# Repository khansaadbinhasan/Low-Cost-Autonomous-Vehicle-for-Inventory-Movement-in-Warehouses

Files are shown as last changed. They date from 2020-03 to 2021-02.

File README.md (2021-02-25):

# Low-Cost Autonomous Vehicle for Inventory Movement in Warehouses

* [__Project Objectives__](#project-objectives)
* [__Our Model__](#our-model)
* [__Evaluation Parameters__](#evaluation-parameters)
* [__Evaluating Model__](#evaluating-model)
* [__About this repository__](#about-this-repository)
* [__Conclusion and Further work__](#conclusion-and-further-work)
* [__More Information__](#more-information)

## Project Objectives

Automation can help Warehouses become more efficient, productive, robust, and cost-effective. A variety of Autonomous Robots are used in large warehouses which can be expensive. We intend to build cost-effective Autonomous Robots for small and medium scale Warehouses with reasonable accuracy.

## Our Model

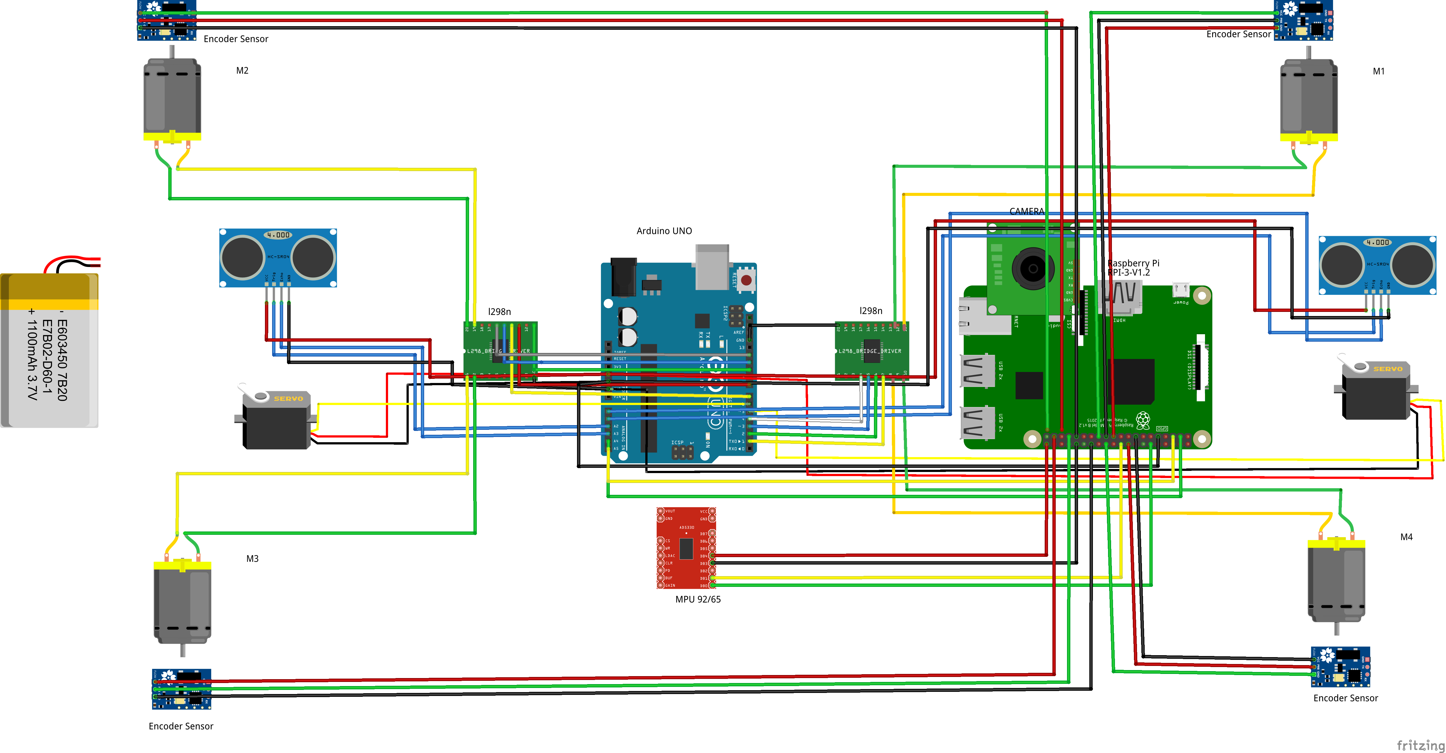
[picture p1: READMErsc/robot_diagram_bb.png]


The robot is monitored by the camera, which sends the stream to the workstation. Using the procedure described below, the workstation sends a command(UP, DOWN, LEFT, RIGHT) to the rpi via a TCP connection. The rpi then sends this command to the Arduino. The Arduino then sends a message to motor drivers accordingly. IMUs and Wheel Encoders are attached to the robot, which sends data to the rpi via an I2C connection. The Arduino is also connected to two servo motors mounted at the front and back. Two ultrasonic sensors are also connected to the servos. This arrangement can be used for backup and collision avoidance.

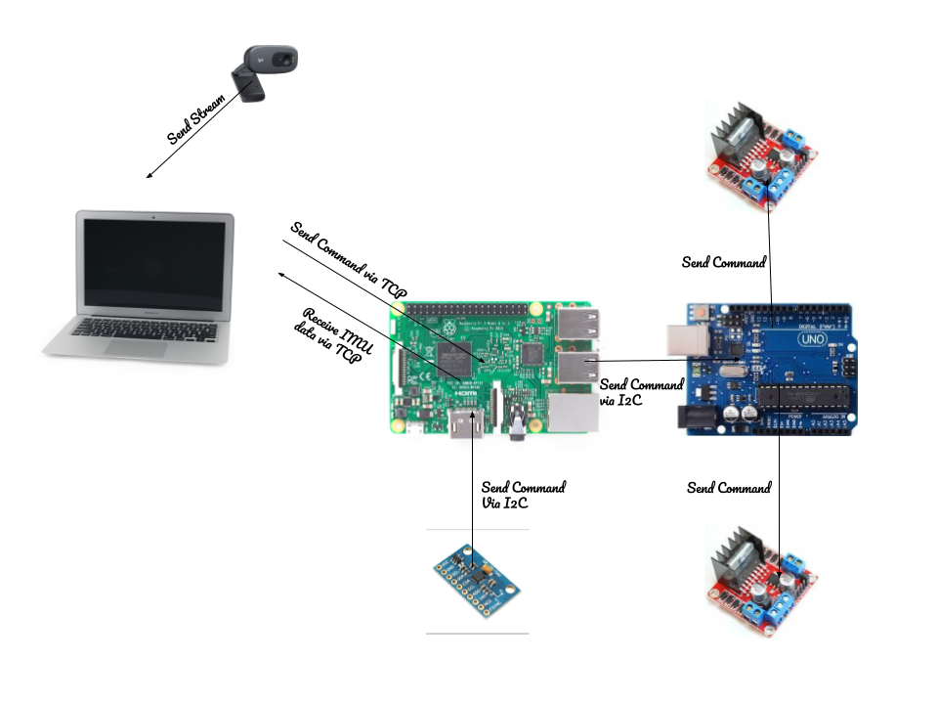
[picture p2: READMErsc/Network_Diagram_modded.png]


The Source and Destination are provided by the user in the environment visible to the camera. A path is made from source to destination using the A-star Algorithm.
A colored marker is placed on the robot which is used to estimate the robot’s location and the heading. A line is drawn from the yellow to the purple marker which gives the Heading. The decision to move the next step is taken using the heading of the robot, the robot’s current location, and the next coordinate in the path to follow. 

<p align="center">
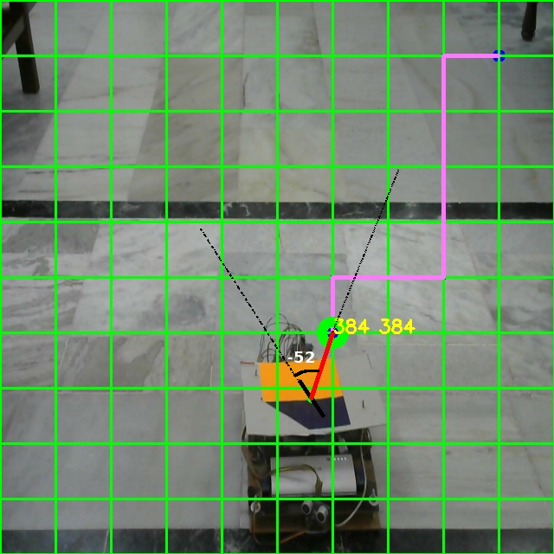
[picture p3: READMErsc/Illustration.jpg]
  
</p>

## Evaluation Parameters

* **Cost and Accuracy:** There is a trade-off between the accuracy of the robot and the cost required to build it. 
* **Scalability:** Using an overhead camera for tracking, robots can easily be scaled up, to track and guide multiple robots.
* **Backup system:** Redundancy should be available that could be used in case of any failure with the primary system. 
* **Path Following and Reaching Destination:** To track the deviation while the robot is traversing the estimated path and check whether the robot can reach the destination or not. 

## Evaluating Model 

We Evaluate the results on the success rate of the robot in reaching the destination and the deviation in the path to reach the destination. We have considered that if the distance between the robot and destination is less than 20cm or 100px, then the robot is on the destination point. We draw the path that the robot should move on and the path that the robot moved on. We compare these paths to measure how close the robot was to the destination.
The computed path is shown in orange color and the actual path traversed by the robot is shown using the blue color. 

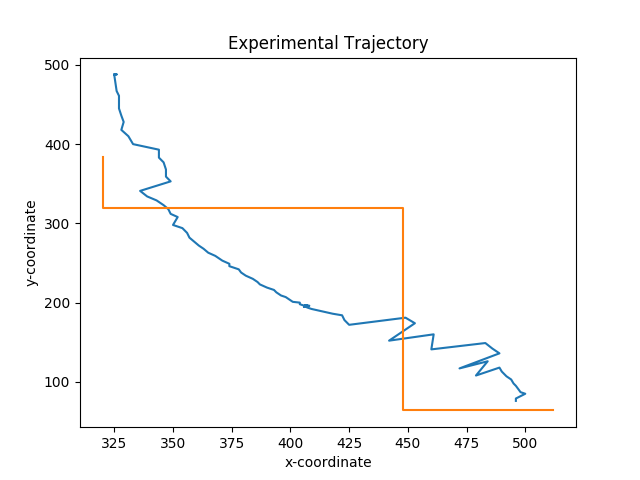
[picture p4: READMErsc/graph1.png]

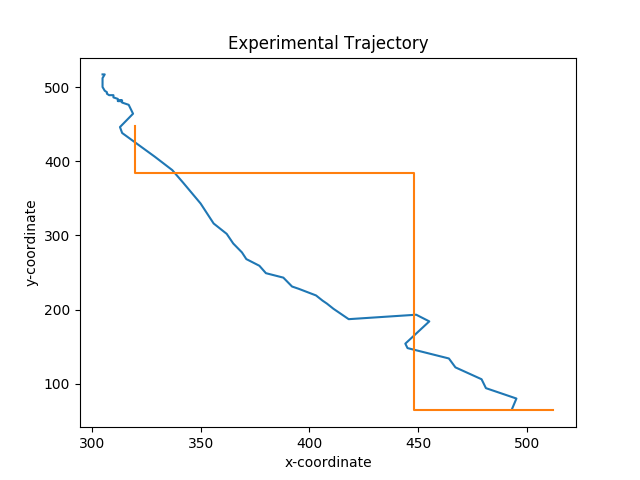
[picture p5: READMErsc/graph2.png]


Out of 10 times, The robot was able to reach the destination 6 times. Hence, the accuracy of our model should be close to 60%. The robot is built with cheap hardware which is easily available making our robot very affordable. The robot also uses an overhead camera which facilitates greater scalability

## About this repository

* **rsc** contains images and other files used for aid in building the model and documenting the work.
* **src** contains the source code of the project consisting of three folders:
	* **Arduino** contains the code to be uploaded to Arduino. Arduino further contains three folders:
		* **Misc Codes** contains code that was used to learn about libraries. Most of these are taken from tutorials easily found online. It also contains code that is no longer used in the robot but was used for testing at some point. It contains code to get data from ultrasonic sensors, move servos, move motors, etc.
		* **libs** contain the libraries that were used in the Arduino Project.
		* **Important** contains the code that was at some point used in the project and still holds importance. It can be used to test various parts of the robot. For example- to move the robot, rotate ultrasonic sensors, etc.

	* **Workstation** contains two folders:
		* **Important** contains the final code that was used in the workstation. 
		* **Misc Codes** contains code that was used to learn about modules and to test the robot. Some of the code was previously used.

	* **rpi** contains two folders:
		* **Important** contains the final code that was used in the raspberry pi.
		* **Misc Codes** contains code that was used to learn about modules and to test the robot. Some of the code was previously used.

* Upload `Major-Project/src/Arduino/important/MotionWithRotatingHCSR04/MotionWithRotatingHCSR04.ino` to Arduino UNO.
* Upload `src/rpi/Important/master.py` to raspberry pi and run it. This would wait for a connection to the address specified in the code. 
* Connect a camera to the workstation and place it so that the robot is clearly visible.
* Run `Major-Project/src/Workstation/Important/Obstacle Detection and Path Planning/main2.py`, you may want to configure the `IP address` and `port` in `parameters.py` as well. 
* A window will appear showing the stream from the camera. Double-click on the window at the starting point of the robot and the destination. Press `Esc`. Now a path appears and the robot starts moving toward the destination. The robot should move as shown in [this video](https://www.youtube.com/watch?v=GJ0nYhXhNK4&list=PLMkePoybCpm4CkMRtGrQV7CXr9gtPblFH&index=5)

## Conclusion and Further work

We have built a cheap and fairly accurate robot. It is versatile and can work in varied environments. Given the backup system and an overhead camera, the robot is fairly secure and scalable. The scope of the work can be enhanced in the future by employing novel ways of increasing accuracy with little changes in cost.

## More Information

* Please see my [Project Report](https://docs.google.com/document/d/1Ga6hZdya4-FO2D3pxWp_QicPi5e_mkiPZHorXCSN8MU/edit?usp=sharing) for more detailed information about this project. 
* A paper was also published in [PDGC 2020](https://www.juit.ac.in/pdgc-2020/index1.php) titled _**"Low-Cost Autonomous Vehicle for Inventory Movement in Warehouses"**_ You can Find it [here](https://ieeexplore.ieee.org/document/9315762). Please cite as `F. Alam, K. S. Bin Hasan and A. Varshney, "Low-Cost Autonomous Vehicle for Inventory Movement in Warehouses," 2020 Sixth International Conference on Parallel, Distributed and Grid Computing (PDGC), Waknaghat, India, 2020, pp. 400-405, doi: 10.1109/PDGC50313.2020.9315762.`
* Please refer to [this playlist](https://www.youtube.com/playlist?list=PLMkePoybCpm4CkMRtGrQV7CXr9gtPblFH) to learn more about the robot.
* You can also find the [presentation for the paper](https://www.slideshare.net/khansaadbinhasan/lowcost-autonomous-vehicle-for-inventory-movement-in-warehouses)

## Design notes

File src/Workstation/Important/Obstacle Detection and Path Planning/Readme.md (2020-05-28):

Dependencies to install <br/>
python3 -m pip install --user opencv-contrib-python</br>
<br/>
Steps <br/>
1. To run - python3 main2.py<br/>
2. It will ask the grid size, frame height, ,frame width, whether you want to detect obstacle in that frame or not.
3. Then select the two points one as source and other as destination<br/>
4. Black colour objects will be treated as obstacles.<br/>
5. Then the next window will be opened, with the help of the mouse pointer,  select the region of the frame that you want to track and then press enter<br/>

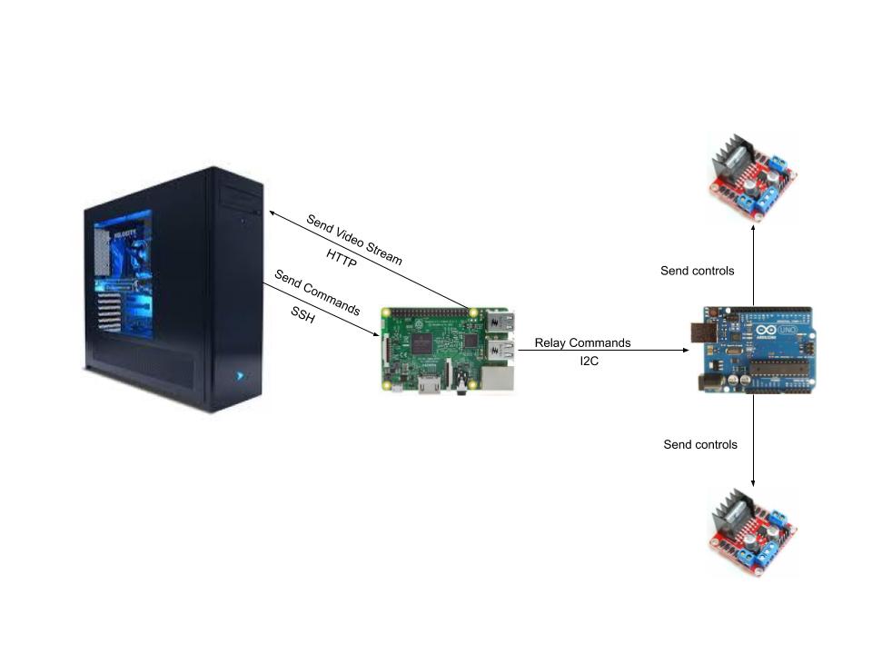
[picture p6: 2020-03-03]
rsc/System Overview.jpg

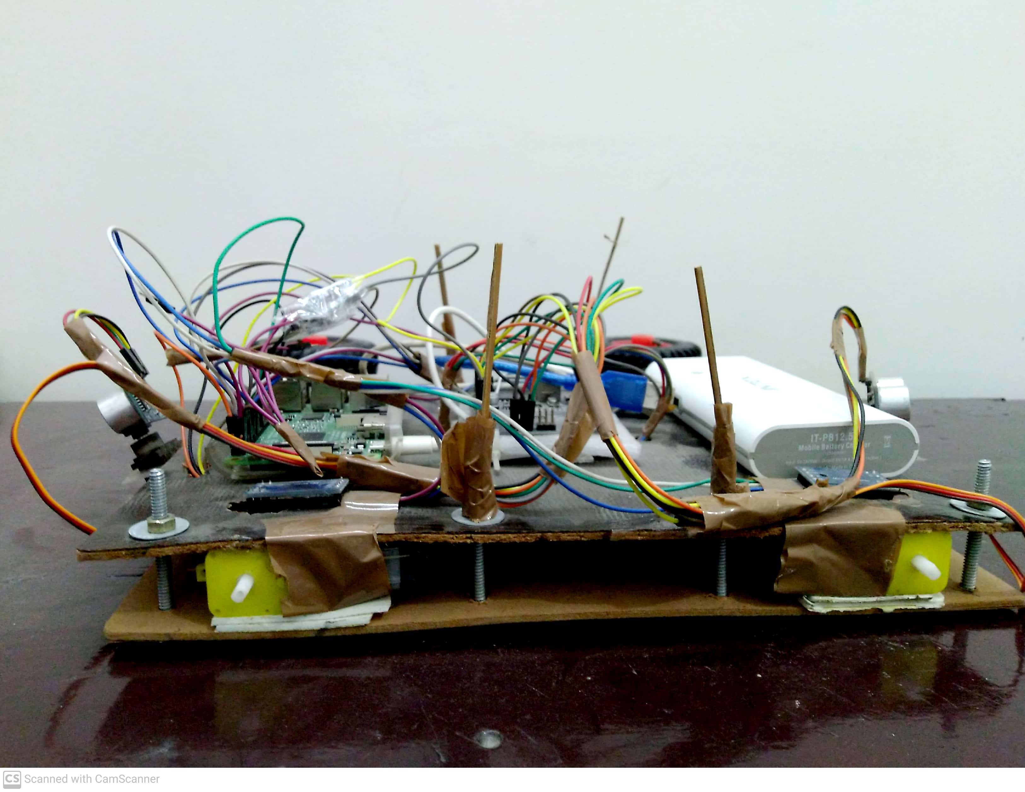
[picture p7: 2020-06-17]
rsc/Photos/project_2.jpg

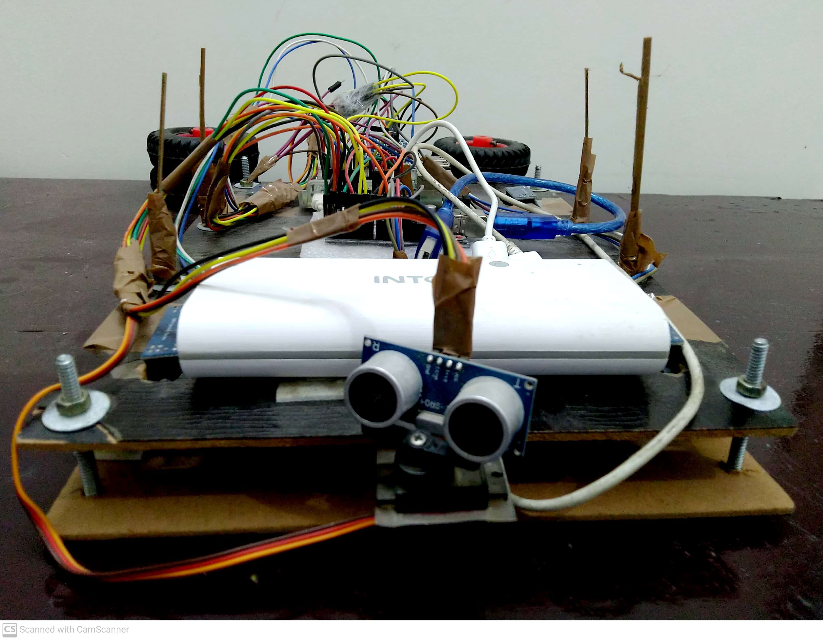
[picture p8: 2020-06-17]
rsc/Photos/project_3.jpg

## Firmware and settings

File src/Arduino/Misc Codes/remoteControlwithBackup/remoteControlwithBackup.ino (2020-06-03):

/*
  --> Uses A4 and A5 pins of arduino and connects according to /rsc/i2c.jpg
  --> This sketch helps in I2C communication with the raspberry pi, receives command from the pi and sends ACK to it
  --> This sketch runs motors in different directions according to commands received via I2C from rpi.
  --> After setting up the Robot, upload this sketch to arduino.
  --> This can be used to test if remote control is working or not
*/

/*  Temperature(*C) Table for ultrasonic sound

Temp, T(*C)     Speed, v(m/s)

T < 10        331 + 0.6*T
10 < T < 20     331 + 0.6*T
20 < T < 30     331 + 0.6*T
30 < T < 40     331 + 0.6*T
40 < T < 50     331 + 0.6*T
Over          336 + 0.1*T

*/


#include <Servo.h>
#include <Wire.h>

#define SLAVE_ADDRESS 0x04


Servo servo_forward;
Servo servo_backward;


// pin numbers for HC-SR04, 1 is front, 2 is back
#define trigPin_backward A0
#define echoPin_backward A1

#define trigPin_forward A2
#define echoPin_forward A3

#define powerPin 9


// pin numbers for Servos, 1 is front, 2 is back
#define servoPin_forward 5
#define servoPin_backward 6


// variables

// Defining different directions for the robot
const int forward = 1;
const int backward = 2;

// commands to move the robot in different directions
int STOP = 0;
int UP = 1;
int DOWN = 2;
int RIGHT = 3;
int LEFT = 4;

int cmd = STOP;


// motor driver front
// motor one
int input_front1 = 2;
int input_front2 = 4;


// motor two
int input_front3 = 7;
int input_front4 = 8;


// motor driver 2
// motor three
int input_back3 = 12;
int input_back4 = 13;


// motor four
int input_back1 = 10;
int input_back2 = 11;


// Variables for HC-SR04 sensor
long duration_backward;
int distance_backward;
long duration_forward;
int distance_forward;

int currentTemp = 25;
const int v = 331 + 0.6*currentTemp;
const int upper_HCSR04_limit = 400;
const int lower_HCSR04_limit = 2;


// Variables for Servo
// const int defaultAng = 90;
const int minAng = 0;
const int maxAng = 180;
const int midAng = ( maxAng - minAng ) / 2;

int servoang_front = midAng;
int servoang_back = midAng;

int i = 0;
int j = 0;


// For Backup
int safetyDist = 10;
int robotSafe = 1;
int letRun = 0;
int wireIn = -1;

void setup() 
{
  //Setting up the I2C connections
  Wire.begin(SLAVE_ADDRESS);
  Wire.onReceive(receiveData);
  Wire.onRequest(sendData);


  //motor drive 1
  // motor 1
  pinMode(input_front1, OUTPUT);
  pinMode(input_front2, OUTPUT);
  
  // motor 2
  pinMode(input_front3, OUTPUT);
  pinMode(input_front4, OUTPUT);


  //motor drive 2
  // motor 3
  pinMode(input_back3, OUTPUT);
  pinMode(input_back4, OUTPUT);
  
  // motor 4
  pinMode(input_back1, OUTPUT);
  pinMode(input_back2, OUTPUT);


  //HCSR04 pins, 1 is front 2 is back
  pinMode(trigPin_backward, OUTPUT); // Sets the trigPin as an Output
  pinMode(echoPin_backward, INPUT); // Sets the echoPin as an Input

  pinMode(trigPin_forward, OUTPUT); // Sets the trigPin as an Output
  pinMode(echoPin_forward, INPUT); // Sets the echoPin as an Input

  pinMode(powerPin, OUTPUT); // Sets the echoPin as an Input


  //Servo pins, 1 is front 2 is back
  servo_forward.attach(servoPin_forward, minAng, maxAng );
  servo_backward.attach(servoPin_backward, minAng, maxAng );

  Serial.begin(115200); // Starts the serial communication
}



void update_distances()
{
  // Clears the trigPin
  digitalWrite(trigPin_backward, LOW);
  delayMicroseconds(2);

  // Sets the trigPin on HIGH state for 10 micro seconds
  digitalWrite(trigPin_backward, HIGH);
  delayMicroseconds(10);
  digitalWrite(trigPin_backward, LOW);

  // Reads the echoPin, returns the sound wave travel time in microseconds
  duration_backward = pulseIn(echoPin_backward, HIGH);

  // Calculating the distance in cm
  distance_backward = duration_backward*v/(2*10000);

  delayMicroseconds(2);



  // Clears the trigPin
  digitalWrite(trigPin_forward, LOW);
  delayMicroseconds(2);

  // Sets the trigPin on HIGH state for 10 micro seconds
  digitalWrite(trigPin_forward, HIGH);
  delayMicroseconds(10);
  digitalWrite(trigPin_forward, LOW);

  // Reads the echoPin, returns the sound wave travel time in delayMicroseconds
  duration_forward = pulseIn(echoPin_forward, HIGH);

  // Calculating the distance in cm
  distance_forward = duration_forward*v/(2*10000);



    // Prints the distance on the Serial Monitor
    
  if( distance_backward > upper_HCSR04_limit || distance_backward < lower_HCSR04_limit )
  {
    distance_backward = -1;
    Serial.println("backward distance is out of range.");
    Serial.print(distance_backward);
  }

  else
  {
    Serial.print("Backward Distance: ");
    Serial.print(distance_backward);
    Serial.println(" cm");
  }


  if( distance_forward > upper_HCSR04_limit || distance_forward < lower_HCSR04_limit )
  {
    distance_forward = -1;
    Serial.println("forward distance is out of range.");
    Serial.print(distance_forward);
  }

  else
  {   
    Serial.print("Forward Distance: ");
    Serial.print(distance_forward);
    Serial.println(" cm\n\n");
  }
}

// void reset_variables()
// {
//   int servoang_front = midAng;
//   int servoang_back = midAng;

//   // int forward_movement = 2;
//   // int backward_movement = 2;

//   update_distances();
// }


// void rotate_servo_left(int servo_num)
// {
//   if( servo_num == 1 )
//   {
//     servo_forward.write(midAng);

//     for(i = midAng; i < maxAng; i++)
//     {
//       servo_forward.write(i);  // tell servo to go to a particular angle
//       update_distances();
//       delay(10);
//     }
//   } 


//   if( servo_num == 2 )
//   {
//     servo_backward.write(midAng);

//     for(i = midAng; i < maxAng; i++)
//     {
//       servo_backward.write(i);  // tell servo to go to a particular angle
//       update_distances();
//       delay(10);
//     }

//   } 
// }

// void rotate_servo_right(int servo_num)
// {
//   if( servo_num == 1 )
//   {
//     servo_forward.write(midAng);

//     for(i = midAng; i > minAng; i--)
//     {
//       servo_forward.write(i);  // tell servo to go to a particular angle
//       update_distances();
//       delay(10);
//     }
//   } 


//   if( servo_num == 2 )
//   {
//     servo_backward.write(midAng);

//     for(i = midAng; i > minAng; i--)
//     {
//       servo_backward.write(i);  // tell servo to go to a particular angle
//       update_distances();
//       delay(10);
//     }

//   } 
// }




// this function will run all the motors in forward direction
// parameter delayTime indicates the time for which we want to execute the command
void move_forward( int delayTime )
{
  //assigning input directions to motor driver 1
//  stop(1000);
//  delay(500);
  
  // motor 1
  digitalWrite(input_front1, LOW);
  digitalWrite(input_front2, HIGH); 
  
  //motor 2
  digitalWrite(input_front3, LOW);
  digitalWrite(input_front4, HIGH);

  delay(500);

  //assigning input directions to motor driver 2
  
  //motor 3
  digitalWrite(input_back3, LOW);
  digitalWrite(input_back4, HIGH); 
  
  //motor 4
  digitalWrite(input_back1, LOW);
  digitalWrite(input_back2, HIGH);

  delay(delayTime);
}


// this function will run all the motors in backward direction
// parameter delayTime indicates the time for which we want to execute the command
void move_backward(int delayTime)
{
  // Executing this function resulted in shutting off of powerbank, most likely reason maybe since we were not only making high pins to low but also low to high
  // This may have resulted in a lot of usage of current, Hence, we first stop the robot so that current used is less. This seems to work for this particular case.
  stop(1000);

//  delay(500);

  
  //assigning input directions to motor driver 1
  
  // motor 1
  digitalWrite(input_front1, HIGH);
  digitalWrite(input_front2, LOW); 
  
  //motor 2
  digitalWrite(input_front3, HIGH);
  digitalWrite(input_front4, LOW);


  delay(500);

  //assigning input directions to motor driver 2
  
  //motor 3
  digitalWrite(input_back3, HIGH);
  digitalWrite(input_back4, LOW); 
  
  //motor 4
  digitalWrite(input_back1, HIGH);
  digitalWrite(input_back2, LOW);

  delay(delayTime);

}


// this function will run right motors in forward direction
// parameter delayTime indicates the time for which we want to execute the command
void move_right(int delayTime)
{
  //assigning input directions to motor driver 1
  
  // motor 1
  digitalWrite(input_front1, LOW);
  digitalWrite(input_front2, LOW); 
  
  //motor 2
  digitalWrite(input_front3, LOW);
  digitalWrite(input_front4, HIGH);



  //assigning input directions to motor driver 2
  
  //motor 3
  digitalWrite(input_back3, LOW);
  digitalWrite(input_back4, LOW); 
  
  //motor 4
  digitalWrite(input_back1, LOW);
  digitalWrite(input_back2, HIGH);

  delay(delayTime);
}


// this function will run left motors in forward direction
// parameter delayTime indicates the time for which we want to execute the command
void move_left(int delayTime)
{
  //assigning input directions to motor driver 1
  
  // motor 1
  digitalWrite(input_front1, LOW);
  digitalWrite(input_front2, HIGH); 
  
  //motor 2
  digitalWrite(input_front3, LOW);
  digitalWrite(input_front4, LOW);



  //assigning input directions to motor driver 2
  
  //motor 3
  digitalWrite(input_back3, LOW);
  digitalWrite(input_back4, HIGH); 
  
  //motor 4
  digitalWrite(input_back1, LOW);
  digitalWrite(input_back2, LOW);

  delay(delayTime);
}


// this function will stop all motors
// parameter delayTime indicates the time for which we want to execute the command
void stop(int delayTime)
{
  
  //assigning input directions to motor driver 1
  
  // motor 1
  digitalWrite(input_front1, LOW);
  digitalWrite(input_front2, LOW); 
  
  //motor 2
  digitalWrite(input_front3, LOW);
  digitalWrite(input_front4, LOW);


  //assigning input directions to motor driver 2
  
  //motor 3
  digitalWrite(input_back3, LOW);
  digitalWrite(input_back4, LOW); 
  
  //motor 4
  digitalWrite(input_back1, LOW);
  digitalWrite(input_back2, LOW);  

  delay(delayTime);
}


// Function to receive commands from rpi and move the robot accordingly
void receiveData(int byteCount) 
{

  Serial.print("recieving commands");

  servo_forward.write(midAng);
  servo_backward.write(midAng);

  while (Wire.available()) 
  {
    wireIn = Wire.read();

    

    if( wireIn == UP || wireIn == DOWN || wireIn == LEFT || wireIn == RIGHT || wireIn == STOP )
    {
      cmd = wireIn;

      Serial.print("command received: ");

      
      Serial.println(cmd);


      Serial.print("letrun: ");
      Serial.println(letRun);

      if( letRun )
      {

        if (cmd == UP) 
        {
          move_forward(1000);
        } 

        else if (cmd == DOWN) 
        {
          move_backward(1000);
        } 

        else if (cmd == RIGHT) 
        {
          move_right(1000);
        } 

        else if (cmd == LEFT) 
        {
          move_left(1000);
        } 

        else 
        {
          stop(5000);
        }

        delay(1000);
      }
    }

  }

}

void sendData() 
{
  Wire.write(wireIn);
}

void check_obstacle_take_action()
{
  update_distances();

  if( distance_forward < safetyDist )
  {
    stop(1);

    if( cmd == UP )
    {
      Serial.println("Command may lead to collision. Overriding. Initiating backup sequence....");
      letRun = 0;
      backup_algo();
    }

    else if( cmd == RIGHT || cmd == LEFT && distance_forward != -1 )
      letRun = 1;

  }

  if( distance_backward < safetyDist )
  {
    stop(1);

    if( cmd == DOWN )
    {
      Serial.println("Command may lead to collision. Overriding. Initiating backup sequence....");
      letRun = 0;
      backup_algo();
    }

    else if(distance_backward != -1)
      letRun = 1;
  }

  if( distance_forward > safetyDist || distance_backward > safetyDist )
    letRun = 1;

}

// void backup_algo()
// {
//   if( distance_forward < safetyDist )
//   {
//     int spaceFound = 0;
//     servoang_front = midAng;

//     while( !spaceFound )
//     {
//       servo_forward.write(servoang_front);
//       update_distances();
//       delay(10);      

//       if(distance_forward > safetyDist)
//         spaceFound = 1;

//       if(servoang_front != maxAng)
//         servoang_front++;

//       else
//       {
//         Serial.println("No path found on the right.");
//         break;
//       }

//     }

//     if( spaceFound )
//     {
//       servo_forward.write(midAng);
//       update_distances();

//       while( distance_forward < safetyDist )
//       {
//         move_right(100);
//         update_distances();
//       }

      
//       robotSafe = 0;

//       while(!robotSafe)      
//       {
//         move_forward(1000);
//         update_distances();

//         if( distance_forward > safetyDist && distance_backward > safetyDist )
//         {
//           Serial.println("Robot now safe backup algo aborting....");
//           stop(1);
//           servo_forward.write(midAng);
//           servo_backward.write(midAng);
//           update_distances();
//           robotSafe = 1;
//           return;
//         }
//       }
//     }

//     if( !spaceFound )
//       Serial.println("Looking for Path on Left");

//     servoang_front = midAng;

//     while( !spaceFound )
//     {
//       servo_forward.write(servoang_front);
//       update_distances();
//       delay(10);      

//       if(distance_forward > safetyDist)
//         spaceFound = 1;

//       if(servoang_front != minAng)
//         servoang_front--;

//       else
//       {
//         Serial.println("No path found on the left.");
//         break;
//       }

//     }

//     if( spaceFound )
//     {
//       servo_forward.write(midAng);
//       update_distances();

//       while( distance_forward < safetyDist )
//       {
//         move_left(100);
//         update_distances();
//       }

//       robotSafe = 0;

//       while(!robotSafe)      
//       {
//         move_forward(1000);
//         update_distances();

//         if( distance_forward > safetyDist && distance_backward > safetyDist )
//         {
//           Serial.println("Robot now safe backup algo aborting....");
//           robotSafe = 1;
//           stop(1);
//           servo_forward.write(midAng);
//           servo_backward.write(midAng);
//           update_distances();
//           return;
//         }
//       }
//     }

//   }


//   if( distance_backward < safetyDist )
//   {
//     int spaceFound = 0;
//     servoang_back = midAng;

//     while( !spaceFound )
//     {
//       servo_backward.write(servoang_back);
//       update_distances();
//       delay(10);      

//       if(distance_backward > safetyDist)
//         spaceFound = 1;

//       if(servoang_back != maxAng)
//         servoang_back++;

//       else
//       {
//         Serial.println("No path found on the right.");
//         break;
//       }

//     }

//     if( spaceFound )
//     {
//       servo_backward.write(midAng);
//       update_distances();

//       while( distance_backward < safetyDist )
//       {
//         move_left(100);
//         update_distances();
//       }

      
//       robotSafe = 0;

//       while(!robotSafe)      
//       {
//         move_backward(1000);
//         update_distances();

//         if( distance_forward > safetyDist && distance_backward > safetyDist )
//         {
//           Serial.println("Robot now safe backup algo aborting....");
//           stop(1);
//           servo_forward.write(midAng);
//           servo_backward.write(midAng);
//           update_distances();

//           robotSafe = 1;
//           return;
//         }
//       }
//     }

//     if( !spaceFound )
//       Serial.println("Looking for Path on Left");


//     spaceFound = 0;
//     servoang_back = midAng;

//     while( !spaceFound )
//     {
//       servo_backward.write(servoang_back);
//       update_distances();
//       delay(10);      

//       if(distance_backward > safetyDist)
//         spaceFound = 1;

//       if(servoang_back != minAng)
//         servoang_back--;

//       else
//       {
//         Serial.println("No path found on the left.");
//         break;
//       }

//     }

//     if( spaceFound )
//     {
//       servo_backward.write(midAng);
//       update_distances();

//       while( distance_backward < safetyDist )
//       {
//         move_right(100);
//         update_distances();
//       }

      
//       robotSafe = 0;

//       while(!robotSafe)      
//       {
//         move_backward(1000);
//         update_distances();

//         if( distance_forward > safetyDist && distance_backward > safetyDist )
//         {
//           Serial.println("Robot now safe backup algo aborting....");
//           stop(1);
//           servo_forward.write(midAng);
//           servo_backward.write(midAng);
//           update_distances();
//           robotSafe = 1;
//           return;
//         }
//       }
//     }

//     if( !spaceFound )
//       Serial.println("No path found");

//   }
// }
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
void loop() 
{
  digitalWrite(powerPin, HIGH);
  update_distances();

  servo_forward.write(midAng);
  servo_backward.write(midAng);

  letRun = 0;
  check_obstacle_take_action();

  delay(100);
}

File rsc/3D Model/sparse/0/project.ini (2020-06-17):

log_to_stderr=false
log_level=2
database_path=/mnt/sda3/home/kringata/Desktop/College Stuff/Major Project/rsc/3D Model/database.db
image_path=/mnt/sda3/home/kringata/Desktop/College Stuff/Major Project/rsc/3D Model/images
[ImageReader]
single_camera=false
default_focal_length_factor=1.2
camera_model=SIMPLE_RADIAL
camera_params=
[SiftExtraction]
use_gpu=true
estimate_affine_shape=false
upright=false
domain_size_pooling=false
num_threads=4
max_image_size=2400
max_num_features=8192
first_octave=-1
num_octaves=4
octave_resolution=3
max_num_orientations=2
dsp_num_scales=10
peak_threshold=0.0066666666666666671
edge_threshold=10
dsp_min_scale=0.16666666666666666
dsp_max_scale=3
gpu_index=0
[SiftMatching]
use_gpu=true
cross_check=true
multiple_models=false
guided_matching=false
num_threads=4
max_num_matches=32768
max_num_trials=10000
min_num_inliers=15
max_ratio=0.80000000000000004
max_distance=0.69999999999999996
max_error=4
confidence=0.999
min_inlier_ratio=0.25
gpu_index=0
[SequentialMatching]
quadratic_overlap=true
loop_detection=false
overlap=5
loop_detection_period=10
loop_detection_num_images=30
loop_detection_num_verifications=0
loop_detection_max_num_features=-1
vocab_tree_path=
[SpatialMatching]
is_gps=true
ignore_z=true
max_num_neighbors=50
max_distance=100
[BundleAdjustment]
refine_focal_length=true
refine_principal_point=false
refine_extra_params=true
max_num_iterations=100
max_linear_solver_iterations=200
function_tolerance=0
gradient_tolerance=0
parameter_tolerance=0
[Mapper]
ignore_watermarks=false
multiple_models=true
extract_colors=true
ba_refine_focal_length=true
ba_refine_principal_point=false
ba_refine_extra_params=true
ba_global_use_pba=true
tri_ignore_two_view_tracks=true
min_num_matches=15
max_num_models=50
max_model_overlap=20
min_model_size=10
init_image_id1=-1
init_image_id2=-1
init_num_trials=200
num_threads=4
ba_local_num_images=6
ba_local_max_num_iterations=25
ba_global_pba_gpu_index=-1
ba_global_images_freq=500
ba_global_points_freq=250000
ba_global_max_num_iterations=50
ba_global_max_refinements=5
ba_local_max_refinements=2
snapshot_images_freq=0
init_min_num_inliers=100
init_max_reg_trials=2
abs_pose_min_num_inliers=30
max_reg_trials=3
tri_max_transitivity=1
tri_complete_max_transitivity=5
tri_re_max_trials=1
min_focal_length_ratio=0.10000000000000001
max_focal_length_ratio=10
max_extra_param=1.7976931348623157e+308
ba_global_images_ratio=1.1000000000000001
ba_global_points_ratio=1.1000000000000001
ba_global_max_refinement_change=0.00050000000000000001
ba_local_max_refinement_change=0.001
init_max_error=4
init_max_forward_motion=0.94999999999999996
init_min_tri_angle=16
abs_pose_max_error=12
abs_pose_min_inlier_ratio=0.25
filter_max_reproj_error=4
filter_min_tri_angle=1.5
tri_create_max_angle_error=2
tri_continue_max_angle_error=2
tri_merge_max_reproj_error=4
tri_complete_max_reproj_error=4
tri_re_max_angle_error=5
tri_re_min_ratio=0.20000000000000001
tri_min_angle=1.5
snapshot_path=
[DenseStereo]
geom_consistency=true
filter=true
write_consistency_graph=false
max_image_size=2400
window_radius=5
window_step=1
num_samples=15
num_iterations=5
filter_min_num_consistent=2
depth_min=-1
depth_max=-1
sigma_spatial=-1
sigma_color=0.20000000298023224
ncc_sigma=0.60000002384185791
min_triangulation_angle=1
incident_angle_sigma=0.89999997615814209
geom_consistency_regularizer=0.30000001192092896
geom_consistency_max_cost=3
filter_min_ncc=0.10000000149011612
filter_min_triangulation_angle=3
filter_geom_consistency_max_cost=1
cache_size=32
gpu_index=0
[Render]
adapt_refresh_rate=true
image_connections=false
min_track_len=3
refresh_rate=1
projection_type=0
max_error=2
[ExhaustiveMatching]
block_size=50
[VocabTreeMatching]
num_images=100
num_verifications=0
max_num_features=-1
vocab_tree_path=
match_list_path=
[TransitiveMatching]
batch_size=1000
num_iterations=3
[DenseFusion]
max_image_size=2400
min_num_pixels=5
max_num_pixels=10000
max_traversal_depth=100
check_num_images=50
max_reproj_error=2
max_depth_error=0.0099999997764825821
max_normal_error=10
cache_size=32
[DenseMeshing]
depth=13
num_threads=4
point_weight=1
color=32
trim=10

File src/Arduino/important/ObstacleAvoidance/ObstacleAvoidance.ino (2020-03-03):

/*
  --> This sketch runs motors in different directions.
  --> After setting up the Robot, upload this sketch to arduino.
  --> This can be used to test if motors are working correctly or not and also if the robot is executing steering commands correctly(e.g, on different surfaces)
*/

// motor driver 1
// motor one
const int input11 = 2;
const int input12 = 4;


// motor two
const int input13 = 7;
const int input14 = 8;


// motor driver 2
// motor three
const int input23 = 12;
const int input24 = 13;


// motor four
const int input21 = 10;
const int input22 = 11;


void setup()
{
  //motor drive 1
  // motor 1
  pinMode(input11, OUTPUT);
  pinMode(input12, OUTPUT);
  
  // motor 2
  pinMode(input13, OUTPUT);
  pinMode(input14, OUTPUT);


  //motor drive 2
  // motor 3
  pinMode(input23, OUTPUT);
  pinMode(input24, OUTPUT);
  
  // motor 4
  pinMode(input21, OUTPUT);
  pinMode(input22, OUTPUT);

  Serial.begin(9600);

}


// this function will run all the motors in forward direction
// parameter delayTime indicates the time for which we want to execute the command
void move_forward( int delayTime )
{
  //assigning input directions to motor driver 1
  
  // motor 1
  digitalWrite(input11, HIGH);
  digitalWrite(input12, LOW); 
  
  //motor 2
  digitalWrite(input13, HIGH);
  digitalWrite(input14, LOW);



  //assigning input directions to motor driver 2
  
  //motor 3
  digitalWrite(input23, HIGH);
  digitalWrite(input24, LOW); 
  
  //motor 4
  digitalWrite(input21, LOW);
  digitalWrite(input22, HIGH);

  delay(delayTime);
}


// this function will run all the motors in backward direction
// parameter delayTime indicates the time for which we want to execute the command
void move_backward(int delayTime)
{
  // Executing this function resulted in shutting off of powerbank, most likely reason maybe since we were not only making high pins to low but also low to high
  // This may have resulted in a lot of usage of current, Hence, we first stop the robot so that current used is less. This seems to work for this particular case.
  stop(1000);

  
  //assigning input directions to motor driver 1
  
  // motor 1
  digitalWrite(input11, LOW);
  digitalWrite(input12, HIGH); 
  
  //motor 2
  digitalWrite(input13, LOW);
  digitalWrite(input14, HIGH);


  //assigning input directions to motor driver 2
  
  //motor 3
  digitalWrite(input23, LOW);
  digitalWrite(input24, HIGH); 
  
  //motor 4
  digitalWrite(input21, HIGH);
  digitalWrite(input22, LOW);

  delay(delayTime);

}


// this function will run right motors in forward direction
// parameter delayTime indicates the time for which we want to execute the command
void rotate_right(int delayTime)
{
  //assigning input directions to motor driver 1
  
  // motor 1
  digitalWrite(input11, LOW);
  digitalWrite(input12, LOW); 
  
  //motor 2
  digitalWrite(input13, HIGH);
  digitalWrite(input14, LOW);



  //assigning input directions to motor driver 2
  
  //motor 3
  digitalWrite(input23, LOW);
  digitalWrite(input24, LOW); 
  
  //motor 4
  digitalWrite(input21, LOW);
  digitalWrite(input22, HIGH);

  delay(delayTime);
}


// this function will run left motors in forward direction
// parameter delayTime indicates the time for which we want to execute the command
void rotate_left(int delayTime)
{
  //assigning input directions to motor driver 1
  
  // motor 1
  digitalWrite(input11, HIGH);
  digitalWrite(input12, LOW); 
  
  //motor 2
  digitalWrite(input13, LOW);
  digitalWrite(input14, LOW);



  //assigning input directions to motor driver 2
  
  //motor 3
  digitalWrite(input23, HIGH);
  digitalWrite(input24, LOW); 
  
  //motor 4
  digitalWrite(input21, LOW);
  digitalWrite(input22, LOW);

  delay(delayTime);
}


// this function will stop all motors
// parameter delayTime indicates the time for which we want to execute the command
void stop(int delayTime)
{
  
  //assigning input directions to motor driver 1
  
  // motor 1
  digitalWrite(input11, LOW);
  digitalWrite(input12, LOW); 
  
  //motor 2
  digitalWrite(input13, LOW);
  digitalWrite(input14, LOW);


  //assigning input directions to motor driver 2
  
  //motor 3
  digitalWrite(input23, LOW);
  digitalWrite(input24, LOW); 
  
  //motor 4
  digitalWrite(input21, LOW);
  digitalWrite(input22, LOW);  

  delay(delayTime);
}




void loop()
{
  move_forward(2500);
  delay(1000);
  rotate_left(2500);
  delay(1000);
  move_forward(1000);
  delay(1000);
  rotate_right(2500);
  delay(1000);
  move_backward(2500);
  delay(1000);
  stop(10000);
  delay(5000);
}





































// void backup()
// {
//    // update_distances();
//  // decide_and_execute();
//  if( distance1 > safety_dist && distance1 < upper_HCSR04_limit )
//  {
//    // servoang1 = defaultAng;
//    // servoang2 = defaultAng;
//    move_forward(200);
//  }

//  if( distance1 < safety_dist && distance1 > lower_HCSR04_limit )
//  {
//    servoang1 = minAng;

//    while( distance1 < safety_dist && distance1 < upper_HCSR04_limit && servoang1 < maxAng ) 
//    {
//      servoang1++;  
//      update_distances();
//    }

//    if( servoang1 > minAng && servoang1 < midAng )
//    { 
//      while(servoang1 > minAng && servoang1 < midAng && distance1 > safety_dist)
//      {
//        rotate_left(100);
//        update_distances();
//      }

//      if( distance1 < safety_dist )
//      {
//        rotate_right(200);

//        if( distance1 < safety_dist )
//        {
//          forward_movement--;
//        }
//      }

//    }

//    if( servoang1 > midAng && servoang1 < maxAng )
//    {
//      while(servoang1 > midAng && servoang1 < maxAng && distance1 > safety_dist)
//      {
//        rotate_right(100);
//        update_distances();
//      }

//      if( distance1 < safety_dist )
//      {
//        rotate_left(200);

//        if( distance1 < safety_dist )
//        {
//          forward_movement--;
//        }
//      }
//    }

//    if( servoang1 == maxAng && forward_movement == 0 )
//    {
//      Serial.println("forward movement not possible");
//    }

//  }

//  update_distances();

//  if( forward_movement == 0 && distance1 < upper_HCSR04_limit && distance1 > lower_HCSR04_limit )
//  {
//    if( distance2 > safety_dist && distance2 < upper_HCSR04_limit )
//    {
//      servoang1 = defaultAng;
//      servoang2 = defaultAng;
//      move_backward(200);
//    }

//    if( distance2 < safety_dist && distance2 > lower_HCSR04_limit )
//    {
//      servoang2 = minAng;

//      while( distance2 < safety_dist && distance2 < upper_HCSR04_limit && servoang2 < maxAng ) 
//      {
//        servoang2++;  
//        update_distances();
//      }

//      if( servoang2 > minAng && servoang2 < midAng )
//      { 
//        while(servoang2 > minAng && servoang2 < midAng && distance2 > safety_dist)
//        {
//          rotate_right(100);
//          update_distances();
//        }

//        if( distance2 < safety_dist )
//        {
//          rotate_left(200);
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

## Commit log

2020-03-03 reinitialized git repo to remove all heavy files
    [car_diagram.fzz]
2020-05-27 Tested on the model, made changes in socket code, rpi IP, added a file for camera number
2020-05-28 Made frame size same for all windows
2020-05-31 add the grids in the final frame
2020-05-31 Fixed a bug in line 229, which led to out of bound for array qt
    [remoteControl.ino]
2020-05-31 Fixed issues with stopping of car
    [remoteControlNew.ino]
2020-06-15 Made functions for code, added code for imu data
2020-06-15 fixed code for wheel encoders
2020-06-17 Pulling heading code
    [car_diagram.fzz, fusion.cfg, patch-match.cfg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]
